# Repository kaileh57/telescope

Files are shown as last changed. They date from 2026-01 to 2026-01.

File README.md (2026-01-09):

# DIY Newtonian Reflector Telescope

I designed my own telescope!

This is a pretty simple Newtonian Reflector style telescope, with a 114mm primary mirror, and a 25mm secondary mirror. I'm making it because I really love taking pictures of the stars, and was able to do some cool stuff a few weeks ago with a telescope at a family member's house! Hopefully this is a (comparatively) low cost way of getting into the field. There's a couple of great dark sky spots near me (Seattle), and hopefully I can update with some awesome pictures.

Hopefully, I can get some pretty cool images of galaxies and other cool objects, and I've included a barlow lens which should help with planetary photography.

I designed as much as possible myself! Unfortunately I don't have the capabilities to make motors or precision optics, and I'm using a modified version of the Crayford Focuser, as I'm not experienced enough with precision optics.

Crayford focuser: https://www.printables.com/model/125438-125-crayford-focuser-for-telescopes/files

## Assembly

PCB:




CAD:


Annotated CAD:

Azimuth and Altitude motors are connected to the PCB box via pre crimped cables, the Altitude cable should have a significant amount of lose cabling in order to accomodate the rotation of the base. 
The Raspberry PI HQ Camera is mounted to the end of the focuser, and should be attached via ribbon cable to the Raspberry PI Zero 2 W in the electronics enclosure, which is connected to the power management PCB. 
The GPS module should be plugged in to its header on the PCB, and should be placed in a location where it has a good view of the sky, for my configuration, it will be mounted on the side of a truck, and therefor is not practical to include in the CAD model. 
12v DC power comes in to the PCB from the side. 

Approximate limit switch positions, the model here is similar but not identical to the model I already have and am planning to install. The limit switches are wired into the appropriate port on the PCB and are used in calibration so that the telescope knows where its facing. 

Annotated Diagram:
Untitled drawing

**Telescope Focuser**: The 1.25" Crayford focuser design is from [aeberbach on Printables](https://www.printables.com/model/118575-125-crayford-focuser-for-telescopes), licensed under CC BY-NC 4.0.

## License

### Modified MIT License

```
MIT License (with exception)
Copyright (c) 2026 Kellen Heraty

Permission is hereby granted, free of charge, to any person obtaining a copy
of this software and associated documentation files (the "Software"), to deal
in the Software without restriction, including without limitation the rights
to use, copy, modify, merge, publish, distribute, sublicense, and/or sell
copies of the Software, and to permit persons to whom the Software is
furnished to do so, subject to the following conditions:

The above copyright notice and this permission notice shall be included in all
copies or substantial portions of the Software.

EXCEPTION: This license does NOT apply to the 1.25" Crayford focuser design 
files (STL and STEP files in the /focuser directory), which are provided by 
aeberbach under Creative Commons Attribution-NonCommercial 4.0 International 
License (CC BY-NC 4.0). Those files may not be used for commercial purposes.

THE SOFTWARE IS PROVIDED "AS IS", WITHOUT WARRANTY OF ANY KIND, EXPRESS OR
IMPLIED, INCLUDING BUT NOT LIMITED TO THE WARRANTIES OF MERCHANTABILITY,
FITNESS FOR A PARTICULAR PURPOSE AND NONINFRINGEMENT. IN NO EVENT SHALL THE
AUTHORS OR COPYRIGHT HOLDERS BE LIABLE FOR ANY CLAIM, DAMAGES OR OTHER
LIABILITY, WHETHER IN AN ACTION OF CONTRACT, TORT OR OTHERWISE, ARISING FROM,
OUT OF OR IN CONNECTION WITH THE SOFTWARE OR THE USE OR OTHER DEALINGS IN THE
SOFTWARE.
```

## Bill of Materials

### Optics & Camera System

| Category | Item | Qty | Specification | Source | Est. Cost | Link |
|---|---|-----|---|---|---|---|
| Optics | Primary Mirror (spherical) | 1 | 114mm diameter, f/8 (912mm FL), enhanced aluminum coating, BK7 glass, 14mm thick | AliExpress | $25.20 | [Link](https://www.aliexpress.us/item/3256802406856110.html) |
| Optics | Secondary Mirror (flat diagonal) | 1 | 25 minor axis, flat, enhanced aluminum coating | AliExpress | Included | Bundled with primary mirror set |
| Camera | Pi HQ Camera | 1 | Sony IMX477, 12.3MP, C-mount thread | Digikey | $50.00 | [Link](https://www.pishop.us/product/raspberry-pi-hq-camera-cs/?src=raspberrypi) |
| Camera | CSI cable (adapter) | 1 | 500mm length, 22-pin (0.5mm pitch) to 15-pin (1.0mm pitch) | AliExpress | $4.55 | [Link](https://www.aliexpress.us/item/3256808091724799.html) |
| Camera | C-mount to 1.25" adapter | 1 | Short profile, screws onto C-mount, 1.25" barrel slides into focuser | AliExpress | $2.84 | [Link](https://www.aliexpress.us/item/3256803470616922.html) |
| Accessory | 2x Barlow lens with T-ring | 1 | 1.25" barrel, 2x magnification, M42×0.75 T-thread for DSLR | AliExpress | $10.85 | [Link](https://www.aliexpress.us/item/3256802185717221.html) |

### OTA Tube Assembly & Mirror Cell

| Category | Item | Qty | Specification | Source | Est. Cost | Link |
|---|---|-----|---|---|---|---|
| OTA Hardware | Alignment dowel pins | 9 | M3×10mm steel, precision | Hardware Store | $4.00 | M3x10 dowel pins |
| OTA Hardware | Interior flocking material | 1 | Self-adhesive black velvet or flocking paper, ~900×450mm | AliExpress | $8.86 | [Link](https://www.aliexpress.us/item/3256807322733280.html) |
| Mirror Cell | Collimation bolts | 3 | M4×50mm hex head | Hardware Store | $5.00 | M4x50mm hex bolts |
| Mirror Cell | Compression springs | 3 | 0.5mm wire, 5mm od, 10mm long | Hardware Store | $4.00 | Between floor and floating plate for push-pull collimation |
| Mirror Cell | Flat washers (M4) | 6 | M4 size | Hardware Store | $2.00 | Top and bottom of each spring M4x9x0.5 |
| Mirror Cell | Wing nuts | 3 | M4 thread | Hardware Store | $3.50 | Hand-adjustable collimation from below |
| Mirror Cell | Cell mounting screws | 6 | M3×16mm socket head | Hardware Store | $4.50 | Attach cell housing to Segment 1 |
| Mirror Cell | Heat-set inserts (M3) | 6 | M3×6mm×5mm | Hardware Store | $6.00 | Press into Segment 1 for cell mounting |
| Mirror Cell | RTV Silicone | 1 | Sealant | AliExpress | $2.96 | [Link](https://www.aliexpress.us/item/3256807120493463.html) |
| Mirror Cell | Epoxy or super glue | 1 | Small tube | AliExpress | $2.31 | [Link](https://www.aliexpress.us/item/3256809235639574.html) |

### Secondary Spider Assembly

| Category | Item | Qty | Specification | Source | Est. Cost | Link |
|---|---|-----|---|---|---|---|
| Spider | Spider mounting screws | 4 | M3×16mm socket head | - | Included above | Mount spider ring to Segment 4 (through tube wall at 45° offsets) |
| Spider | Spider mounting nuts | 4 | M3 hex nuts | Hardware Store | $2.00 | M3 hex nuts for spider mounting |
| Spider | Secondary mirror adhesive | 1 | RTV silicone | - | Included above | Bonds secondary to 45° holder surface |

### Mount Structure

| Category | Item | Qty | Specification | Source | Est. Cost | Link |
|---|---|-----|---|---|---|---|
| Mount | Tube ring clamp bolts | 2 | M5×50mm hex head | Hardware Store | $4.00 | Clamp tube rings around OTA m5x50 |
| Mount | Tube ring to cradle bolts | 4 | M5×50mm hex head | - | Included above | Attach rings to altitude cradle |
| Mount | Fork to turntable bolts | 4 | M5×25mm socket head | Hardware Store | $3.50 | Secure forks to turntable |
| Mount | M5 nuts | 6 | Standard hex nuts | Hardware Store | $2.50 | For clamp and cradle bolts |
| Mount | M5 washers | 16 | Flat washers | Hardware Store | $3.00 | Under bolt heads and nuts |
| Mount | Heat-set inserts (M5) | 4 | M5 size | Hardware Store | $6.00 | In turntable for fork mounting |
| Mount | Hex nut (1/4-20) | 1 | 1/4-20 UNC thread | Hardware Store | $1.50 | Tripod mount in base center |
| Mount | Felt/foam tape | 1 | Self-adhesive, ~25mm wide roll | AliExpress | $2.24 | [Link](https://www.aliexpress.us/item/3256807381928957.html) |
| Mount | Lazy susan mounting screws | 8 | M4×12mm | Hardware Store | $4.00 | 4 per ring of lazy susan bearing |
| Mount | M4 nuts | 4 | Standard hex nuts | Hardware Store | $2.00 | Inner ring of lazy susan (through-hole to base) |

### Bearings

| Category | Item | Qty | Specification | Source | Est. Cost | Link |
|---|---|-----|---|---|---|---|
| Bearing | 608ZZ bearing | 1 | 8mm ID × 22mm OD × 7mm thick | AliExpress | $4.23 | [Link](https://www.aliexpress.us/item/3256805135171835.html) |
| Bearing | Lazy Susan bearing (Profile B) | 1 | 120mm OD, 79mm ID, 8.5mm thick, aluminum, PCD: 91.8mm inner / 109mm outer | AliExpress | $6.69 | [Link](https://www.aliexpress.us/item/3256807353712714.) |

### Drive Systems

| Category | Item | Qty | Specification | Source | Est. Cost | Link |
|---|---|-----|---|---|---|---|
| Alt Drive | NEMA17 Worm Gear Motor (1:32) | 1 | RobotDigg, 42×42×48mm motor + 40×58×27mm gearbox, 8mm D-shaft output, 1.8Nm torque, 1.7A | AliExpress | $28.06 | [Link](https://www.aliexpress.us/item/3256808139356937.html) |
| Alt Drive | Shaft coupler (8mm-8mm) | 1 | Aluminum, ~25mm body length | AliExpress | $3.49 | [Link](https://www.aliexpress.us/item/3256805451220598.html) |
| Alt Drive | Motor mount screws | 4 | M4×10mm flat head | Hardware Store | $3.00 | - |
| Alt Drive | Mount plate screws | 4 | M4×20mm socket head | Hardware Store | $3.50 | Attach motor mount plate to left fork |
| Az Drive | NEMA17 Worm Gear Motor (1:32) | 1 | RobotDigg, same spec as altitude motor | AliExpress | $28.06 | [Link](https://www.aliexpress.us/item/3256808139356937.html) |
| Az Drive | GT2 timing belt (6mm) | 1 | ~800mm length, open-ended, cut to fit | AliExpress | $8.48 | [Link](https://www.aliexpress.us/item/3256802121511505.html) |
| Az Drive | GT2 pulley (30T) | 1 | 30 teeth, 8mm bore, 6mm belt width | AliExpress | $3.65 | [Link](https://www.aliexpress.us/item/3256805593092055.html) |
| Az Drive | Motor mount screws | 4 | M4×12mm flat head | - | Included above | Through slotted holes in base extension tab |

### PCB Through-Hole Components

| Category | Item | Qty | Specification | Source | Est. Cost | Link |
|---|---|-----|---|---|---|---|
| PCB TH | 100µF 25V electrolytic capacitor | 3 | Through-hole, radial | AliExpress | $2.32 | [Link](https://www.aliexpress.us/item/3256805247425905.html) |
| PCB TH | 220µF 10V electrolytic capacitor | 1 | Through-hole, radial | AliExpress | $2.15 | [Link](https://www.aliexpress.us/item/3256805247425905.html) |
| PCB TH | 2×20 female header | 1 | 2.54mm pitch, through-hole | AliExpress | $1.42 | [Link](https://www.aliexpress.us/item/2251832667900858.html) |
| PCB TH | 1×8 female header | 4 | 2.54mm pitch, through-hole | AliExpress | $1.61 | [Link](https://www.aliexpress.us/item/2255801012106911.html) |
| PCB TH | JST-XH 4-pin connector | 2 | Vertical | - | Included with pigtails kit | Motor output connectors (J_MOT1, J_MOT2) |
| PCB TH | DC barrel jack | 1 | 5.5×2.1mm, center positive | Digikey | $0.64 | [Link](https://www.digikey.com/en/products/detail/same-sky-formerly-cui-devices/PJ-002AH/408446) |

### Electronics Modules

| Category | Item | Qty | Specification | Source | Est. Cost | Link |
|---|---|-----|---|---|---|---|
| Module | Raspberry Pi Zero 2 W | 1 | PI zero 2 w | Digikey | $15.00 | [Link](https://www.digikey.com/en/products/detail/raspberry-pi/SC1176/15298147) |
| Module | TMC2209 StepStick | 2 | BIGTREETECH V1.2 or V1.3 | AliExpress | $9.72 | [Link](https://www.aliexpress.us/item/2255800257311131.html) |
| Module | NEO-6M GPS module | 1 | 3.3V logic output ONLY - 5V will damage Pi! | AliExpress | $8.90 | [Link](https://www.aliexpress.us/item/3256808037885086.html) |
| Module | MP1584 buck converter module | 1 | Adjustable output, set to 5.0-5.1V, needs to be adjustable for precision | AliExpress | $1.57 | [Link](https://www.aliexpress.us/item/3256808313082613.html) |
| Wiring | 22awg wire | 20cm | For connecting MP1584, hard to find in small quantities | AliExpress | $3.04 | [Link](https://www.aliexpress.us/item/3256808757002563.html) |
| Module | 10×10mm heatsinks | 4 | Aluminum, with thermal adhesive tape | AliExpress | $3.94 | [Link](https://www.aliexpress.us/item/3256804749177306.html) |

### Power & Wiring

| Category | Item | Qty | Specification | Source | Est. Cost | Link |
|---|---|-----|---|---|---|---|
| Power | 12V 5A DC power supply | 1 | 5.5×2.1mm barrel jack output, center positive | AliExpress | $17.22 | [Link](https://www.aliexpress.us/item/3256807351095066.html) |
| Wiring | JST-XH 4-pin pigtails | 4 | Pre-crimped leads, ~30cm | AliExpress | $7.13 | [Link](https://www.aliexpress.us/item/3256808528022826.html) |
| Wiring | Heat shrink tubing | 1 | Assorted sizes kit | - | Included | Insulate splices |
| Wiring | Motor cables | 2 | 4-wire, ~50cm, usually included with motors | With motors | Included | Check if included with RobotDigg motors |
| Wiring | Motor extension | 2 | Allows the cables to reach | AliExpress | $6.05 | [Link](https://www.aliexpress.us/item/3256807018820517.html) |

### Accessories

| Category | Item | Qty | Specification | Source | Est. Cost | Link |
|---|---|-----|---|---|---|---|
| Accessory | Rubber friction pads | 4 | Self-adhesive | AliExpress | $2.18 | [Link](https://www.aliexpress.us/item/3256806771014461.html) |

### Focuser Components

| Category | Item | Qty | Specification | Source | Est. Cost | Link |
|---|---|-----|---|---|---|---|
| Motion | MR83ZZ bearings | 4 | 3mm ID × 8mm OD × 3mm thick | AliExpress | $5.24 | [Link](https://www.aliexpress.us/item/3256804648772069.html) |
| Motion | Steel shaft | 1 | 5mm diameter × 90mm length, stainless | AliExpress | $2.31 | [Link](https://www.aliexpress.us/item/3256805290944526.html) |
| Motion | Aluminum flat bar | 1 | 10mm × 3mm × 150mm (cut 64+64+37 = 165mm needed) | AliExpress | $3.52 | [Link](https://www.aliexpress.us/item/3256805124428430.html) |
| Motion | Compression springs | 2 | OD < 5mm, ~6.5mm length, STIFF (not pen springs) | Hardware Store | $3.00 | Small compression springs |
| Inserts | M3 heat-set inserts | 8 | M3 × 5mm L × 4.5mm OD | Hardware Store | $8.00 | M3 heat-set inserts |
| Inserts | M4 heat-set inserts | 4 | M4 × 6mm L × 5.5mm OD | Hardware Store | $6.00 | M4 heat-set inserts |
| Bolts | M3×10mm button head | 4 | Button head, bearing axles | Hardware Store | $3.00 | Button head screws for bearing axles |
| Bolts | M3×12mm socket head | 4 | Socket head, drawtube cap | Hardware Store | $3.00 | Socket head for drawtube cap |
| Bolts | M3×20mm socket head | 4 | Socket head, front cap to base | Hardware Store | $3.50 | Socket head for front cap |
| Bolts | M4×12mm socket head | 4 | Socket head, mount focuser to telescope | - | Included above | - |
| Nuts | M3 nylock nuts | 4 | Nylon insert lock nuts, secure bearing axles | Hardware Store | $2.50 | Nylock nuts for bearing security |
| Nuts | M3 hex nut | 1 | Standard, pressed into front cap for tension screw | - | Included above | - |
| Nuts | M3 thumbscrew | 1 | Knurled head, main tension adjustment | Hardware Store | $3.00 | Knurled thumbscrew for tension |
| Nuts | M3 set screws | 2 | Grub screws | Hardware Store | $2.00 | - |

### 3D Printed Components

Hoping to print all from the same person, near me in Seattle. Mostly PETG, some PLA, TPU would be cool but not needed at all.

| Component | Material | Infill | Est. Print Time | Notes |
|---|---|---|---|---|
| **OTA - Tube Assembly** |
| Tube_Segment_1 (rear) | PETG | 30% gyroid | ~12 hours | Mirror cell interface, 220mm length, 130mm ID, 4mm wall |
| Tube_Segment_2 | PETG | 30% gyroid | ~12 hours | Middle segment, alignment pins at joints |
| Tube_Segment_3 | PETG | 30% gyroid | ~12 hours | Middle segment |
| Tube_Segment_4 (front) | PETG | 30% gyroid | ~12 hours | Focuser boss (70×70mm), spider mount holes at 45° offset |
| **OTA - Mirror Cell (Hadley-style)** |
| Primary_Mirror_Cell_Housing | PETG | 30% | ~8 hours | 154mm OD flange, 120mm ID wall, floor with 40mm vent, 3× spring bosses |
| Floating_Plate | PETG | 30% | ~2 hours | 118mm OD × 8mm, hex pockets for bolt capture, 115mm mirror recess |
| **OTA - Secondary Assembly** |
| Secondary_Spider | PLA or PETG | 40% | ~4 hours | 4-vane design, ring fits inside tube top, 45° mirror holder, 3× collimation screws |
| **OTA - Focuser (aeberbach Crayford - Printables #125438)** |
| Focuser_Body | PETG | 40% | ~2.5 hours | Main body with 4× bearing mounts, 4× M3 insert holes for front cap |
| Pinion_Block | PETG | 40% | ~30 min | Shaft passes through; 2× spring holes in back for tension |
| Front_Cap | PETG | 40% | ~45 min | Recess for M3 hex nut (tension screw); mounts with 4× M3×20mm |
| Drawtube | PETG | 30% | ~1.5 hours | Print flange-down; slots for 2× 64mm aluminum strips |
| Drawtube_Cap | PETG | 30% | ~30 min | Print flange-down; secures aluminum strips; 4× M3×12mm + M3 inserts |
| Pinion_Spacer (×2) | PETG | 30% | ~15 min total | Covers exposed shaft ends outside body |
| Focus_Knob (×2) | PETG | 30% | ~30 min total | Small knob(s) |
| **OTA - Dust Covers** |
| Front_Dust_Cap | PLA or PETG | 20% | ~1 hour | 139mm ID, 145mm OD, 15mm tall with pull tab |
| Rear_Dust_Cover | PLA or PETG | 20% | ~1 hour | 160mm OD disc with 154/148mm retention ring |
| Focuser_Cap | PLA | 20% | ~15 min | 31.5mm plug, 38mm flange, friction fit |
| **Mount - Tube Rings & Cradle** |
| Tube_Ring (×2) | PETG | 30% | ~4 hours total | 148mm OD, 140mm ID, split clamp, mounting boss for cradle |
| Altitude_Cradle | PETG | 30% | ~3 hours | 200×80×8mm plate, LEFT shaft 45mm (motor side), RIGHT shaft 25mm |
| **Mount - Forks** |
| Altitude_Fork_LEFT | PETG | 30% | ~8 hours | 60×120×15mm, 4× M4 heat-set holes for motor mount plate |
| Altitude_Fork_RIGHT | PETG | 30% | ~8 hours | 60×120×15mm, 608ZZ bearing pocket for pivot |
| Alt_Motor_Mount_Plate | PETG | 30% | ~1 hour | 60×60×5mm, NEMA17 pattern, 25mm center clearance hole |
| **Mount - Azimuth Base** |
| Azimuth_Stationary_Base | PETG | 25% | ~12 hours | 280mm dia + motor extension tab (80×70×8mm), tripod mount, lazy susan PCD 91.8mm |
| Azimuth_Turntable | PETG | 25% | ~6 hours | 220mm OD, 80mm center hole, lazy susan PCD 109mm, fork mounting bosses |
| Base_Feet (×4) | PETG or TPU | 30% | ~2 hours | ~40mm tall for gearbox clearance, rubber pad attachment |
| **Electronics** |
| Electronics_Enclosure | PLA | 20% | ~6 hours | Box for PCB + Pi Zero, ventilation slots, friction-fit lid |

### PCB SMT Components (JLCPCB Assembly)

| Designator | Value/Part | LCSC# | Qty/Board | Ext (2 boards) | Notes |
|---|---|---|---|---|---|
| C3 | 22uF 16V Tantalum | C782264 | 1 | $0.67 | Extended |
| C4,C7,C8,C9,C10,C11 | 100nF 0603 | C14663 | 6 | $0.17 | Basic (6× ~$0.03) |
| D1 | 6.8V Zener SOD-123 | C2120 | 1 | $0.26 | Extended |
| F1 | 4A Polyfuse 2920 | C139284 | 1 | $0.61 | Littelfuse Extended |
| F2 | 1.5A Polyfuse 1206 | C70083 | 1 | $0.33 | TECHFUSE Extended |
| Q1 | AO3401A P-FET | C15127 | 1 | $0.11 | Basic |
| R1,R2,R3 | 10k 0603 | C25804 | 3 | $0.02 | Basic |
| U1 | AMS1117-3.3 | C6186 | 1 | $0.32 | Basic |

**SMT Total: $2.49** (from JLCPCB quote)

### Cost Summary

| Source | Total |
|---|---|
| Digikey | $72.69 |
| AliExpress | $285.26 |
| Hardware Store | I will pay/find these parts |
| JLCPCB | $45.71 |
| **Total** | **$403.66** |

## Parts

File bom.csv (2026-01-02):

Category | Item | Qty | Specification | Source | Est. Cost (not incl Shipping or tax) | Link/Notes
OPTICS
Optics | Primary Mirror (spherical) | 1 | 114mm diameter, f/8 (912mm FL), enhanced aluminum coating, BK7 glass, 14mm thick | AliExpress | $25.20 | spherical is much cheaper than parabolic, but slightly worse https://www.aliexpress.us/item/3256802406856110.html
Optics | Secondary Mirror (flat diagonal) | 1 | 25 minor axis, flat, enhanced aluminum coating | AliExpress | Included | Bundled with primary mirror set
CAMERA SYSTEM
Camera | Pi HQ Camera | 1 | Sony IMX477, 12.3MP, C-mount thread | Digikey | $50.00 | https://www.pishop.us/product/raspberry-pi-hq-camera-cs/?src=raspberrypi | SC
Camera | CSI cable (adapter) | 1 | 500mm length, 22-pin (0.5mm pitch) to 15-pin (1.0mm pitch) | AliExpress | $4.55 | 500mm version https://www.aliexpress.us/item/3256808091724799.html
Camera | C-mount to 1.25" adapter | 1 | Short profile, screws onto C-mount, 1.25" barrel slides into focuser | AliExpress | $2.84 | https://www.aliexpress.us/item/3256803470616922.html?
OPTICAL ACCESSORIES
Accessory | 2x Barlow lens with T-ring | 1 | 1.25" barrel, 2x magnification, M42×0.75 T-thread for DSLR | AliExpress | $10.85 | massively helps with planetary imaging https://www.aliexpress.us/item/3256802185717221.html
OTA TUBE ASSEMBLY
OTA Hardware | Alignment dowel pins | 9 | M3×10mm steel, precision | Hardware Store | $4.00 | m3x10 dowel pins
OTA Hardware | Interior flocking material | 1 | Self-adhesive black velvet or flocking paper, ~900×450mm | AliExpress | $8.86 | 45cm x 10m https://www.aliexpress.us/item/3256807322733280.html
PRIMARY MIRROR CELL
Mirror Cell | Collimation bolts | 3 | M4×50mm hex head | Hardware Store | $5.00 | m4x50mm hex bolts
Mirror Cell | Compression springs | 3 | 0.5mm wire, 5mm od, 10mm long | Hardware Store | $4.00 | Between floor and floating plate for push-pull collimation: 0.5mm wire, 5mm od, 10mm long
Mirror Cell | Flat washers (M4) | 6 | M4 size | Hardware Store | $2.00 | Top and bottom of each spring M4x9x0.5
Mirror Cell | Wing nuts | 3 | M4 thread | Hardware Store | $3.50 | Hand-adjustable collimation from below
Mirror Cell | Cell mounting screws | 6 | M3×16mm socket head | Hardware Store | $4.50 | Attach cell housing to Segment 1
Mirror Cell | Heat-set inserts (M3) | 6 | M3×6mm×5mm | Hardware Store | $6.00 | Press into Segment 1 for cell mounting
Mirror Cell | RTV Silicone | 1 | Sealant | AliExpress | $2.96 | Bonds mirror to floating plate; flexible for thermal expansion, https://www.aliexpress.us/item/3256807120493463.html
Mirror Cell | Epoxy or super glue | 1 | Small tube | AliExpress | $2.31 | Permanently captures M4 bolt heads in hex pockets https://www.aliexpress.us/item/3256809235639574.html
SECONDARY SPIDER ASSEMBLY
Spider | Spider mounting screws | 4 | M3×16mm socket head |  | Included above | Mount spider ring to Segment 4 (through tube wall at 45° offsets)
Spider | Spider mounting nuts | 4 | M3 hex nuts | Hardware Store | $2.00 | M3 hex nuts for spider mounting
Spider | Secondary mirror adhesive | 1 | RTV silicone |  | Included above | Bonds secondary to 45° holder surface
MOUNT STRUCTURE
Mount | Tube ring clamp bolts | 2 | M5×50mm hex head | Hardware Store | $4.00 | Clamp tube rings around OTA m5x50
Mount | Tube ring to cradle bolts | 4 | M5×50mm hex head |  | Included above | Attach rings to altitude cradle
Mount | Fork to turntable bolts | 4 | M5×25mm socket head | Hardware Store | $3.50 | Secure forks to turntable
Mount | M5 nuts | 6 | Standard hex nuts | Hardware Store | $2.50 | For clamp and cradle bolts
Mount | M5 washers | 16 | Flat washers | Hardware Store | $3.00 | Under bolt heads and nuts
Mount | Heat-set inserts (M5) | 4 | M5 size | Hardware Store | $6.00 | In turntable for fork mounting
Mount | Hex nut (1/4-20) | 1 | 1/4-20 UNC thread | Hardware Store | $1.50 | Tripod mount in base center
Mount | Felt/foam tape | 1 | Self-adhesive, ~25mm wide roll | AliExpress | $2.24 | Line inside of tube rings to protect OTA, general adhesive, 25mm https://www.aliexpress.us/item/3256807381928957.html
Mount | Lazy susan mounting screws | 8 | M4×12mm | Hardware Store | $4.00 | 4 per ring of lazy susan bearing
Mount | M4 nuts | 4 | Standard hex nuts | Hardware Store | $2.00 | Inner ring of lazy susan (through-hole to base)
BEARINGS
Bearing | 608ZZ bearing | 1 | 8mm ID × 22mm OD × 7mm thick | AliExpress | $4.23 | Altitude pivot (non-motor side, right fork), https://www.aliexpress.us/item/3256805135171835.html
Bearing | Lazy Susan bearing (Profile B) | 1 | 120mm OD, 79mm ID, 8.5mm thick, aluminum, PCD: 91.8mm inner / 109mm outer | AliExpress | $6.69 | Azimuth rotation; https://www.aliexpress.us/item/3256807353712714.
ALTITUDE DRIVE SYSTEM
Alt Drive | NEMA17 Worm Gear Motor (1:32) | 1 | RobotDigg, 42×42×48mm motor + 40×58×27mm gearbox, 8mm D-shaft output, 1.8Nm torque, 1.7A | robotdigg.com | $28.06 | https://www.aliexpress.us/item/3256808139356937.html
Alt Drive | Shaft coupler (8mm-8mm) | 1 | Aluminum, ~25mm body length | AliExpress | $3.49 | Connects motor shaft to cradle pivot shaft, 8x8 https://www.aliexpress.us/item/3256805451220598.html
Alt Drive | Motor mount screws | 4 | M4×10mm flat head | Hardware Store | $3.00
Alt Drive | Mount plate screws | 4 | M4×20mm socket head | Hardware Store | $3.50 | Attach motor mount plate to left fork
AZIMUTH DRIVE SYSTEM
Az Drive | NEMA17 Worm Gear Motor (1:32) | 1 | RobotDigg, same spec as altitude motor | robotdigg.com | $28.06 | https://www.aliexpress.us/item/3256808139356937.html
Az Drive | GT2 timing belt (6mm) | 1 | ~800mm length, open-ended, cut to fit | AliExpress | $8.48 | Wraps around 220mm turntable edge (~690mm circumference), 1m, 6mm width, https://www.aliexpress.us/item/3256802121511505.html
Az Drive | GT2 pulley (30T) | 1 | 30 teeth, 8mm bore, 6mm belt width | AliExpress | $3.65 | Mounts on shaft extension above motor, 30 teeth, 6mm, 8mm bore https://www.aliexpress.us/item/3256805593092055.html
Az Drive | Motor mount screws | 4 | M4×12mm flat head, needs to be flat head for clearance |  | Included above | Through slotted holes in base extension tab
PCB - THROUGH-HOLE COMPONENTS
PCB TH | 100µF 25V electrolytic capacitor | 3 | Through-hole, radial | AliExpress | $2.32 | 1× input bulk + 2× TMC2209 VMOT 25v100uf 6x11 https://www.aliexpress.us/item/3256805247425905.html
PCB TH | 220µF 10V electrolytic capacitor | 1 | Through-hole, radial | AliExpress | $2.15 | 5V rail bulk near Pi header, 10v220uf 5x11 https://www.aliexpress.us/item/3256805247425905.html
PCB TH | 2×20 female header | 1 | 2.54mm pitch, through-hole | AliExpress | $1.42 | Pi Zero socket 1x20pin https://www.aliexpress.us/item/2251832667900858.html
PCB TH | 1×8 female header | 4 | 2.54mm pitch, through-hole | AliExpress | $1.61 | TMC2209 StepStick sockets 1x8pin https://www.aliexpress.us/item/2255801012106911.html
PCB TH | JST-XH 4-pin connector | 2 | vertical |  | Included with pigtails kit | Motor output connectors (J_MOT1, J_MOT2)
PCB TH | DC barrel jack | 1 | 5.5×2.1mm, center positive | Digikey | $0.64 | MUST be from a reliable distributer as we need 12v 5a https://www.digikey.com/en/products/detail/same-sky-formerly-cui-devices/PJ-002AH/408446
ELECTRONICS - MODULES
Module | Raspberry Pi Zero 2 W | 1 | PI zero 2 w | Digikey | $15.00 | Main controller - camera, GPS, motor control, https://www.digikey.com/en/products/detail/raspberry-pi/SC1176/15298147
Module | TMC2209 StepStick | 2 | BIGTREETECH V1.2 or V1.3 | AliExpress | $9.72 | Stepper drivers, 2A max, STEP/DIR mode https://www.aliexpress.us/item/2255800257311131.html
Module | NEO-6M GPS module | 1 | 3.3V logic output ONLY - 5V will damage Pi! | AliExpress | $8.90 | Position and time sync for GoTo https://www.aliexpress.us/item/3256808037885086.html
Module | MP1584 buck converter module | 1 | Adjustable output, set to 5.0-5.1V, needs to be adjustable for precision | AliExpress | $1.57 | 12V to 5V for Pi Zero https://www.aliexpress.us/item/3256808313082613.html
Wiring | 22awg wire | 20cm | For connecting MP1584, hard to find in small quantities | AliExpress | $3.04 | 22 awg https://www.aliexpress.us/item/3256808757002563.html
Module | 10×10mm heatsinks | 4 | Aluminum, with thermal adhesive tape | AliExpress | $3.94 | 1× MP1584 (mandatory!) + 1 for pi + 2× TMC2209 (in case they dont include it) https://www.aliexpress.us/item/3256804749177306.html
POWER
Power | 12V 5A DC power supply | 1 | 5.5×2.1mm barrel jack output, center positive | AliExpress | $17.22 | Minimum 5A for motor peak current headroom, grounded! GST60A12-P1J https://www.aliexpress.us/item/3256807351095066.html
WIRING & CABLES
Wiring | JST-XH 4-pin pigtails | 4 | Pre-crimped leads, ~30cm | AliExpress | $7.13 | https://www.aliexpress.us/item/3256808528022826.html
Wiring | Heat shrink tubing | 1 | Assorted sizes kit |  | included | Insulate splices
Wiring | Motor cables | 2 | 4-wire, ~50cm, usually included with motors | With motors | included | Check if included with RobotDigg motors
Wiring | Motor extension | 2 | allows the cables to reach | AliExpress | $6.05 | https://www.aliexpress.us/item/3256807018820517.html
ACCESSORIES
Accessory | Rubber friction pads | 4 | Self-adhesive | AliExpress | $2.18 | Base feet for stability https://www.aliexpress.us/item/3256806771014461.html
FOCUSER
Motion | MR83ZZ bearings | 4 | 3mm ID × 8mm OD × 3mm thick | AliExpress | $5.24 | Mr83zz 3x8x3mm, order 4, https://www.aliexpress.us/item/3256804648772069.html
Motion | Steel shaft | 1 | 5mm diameter × 90mm length, stainless | AliExpress | $2.31 | 125mm, 5mm diameter https://www.aliexpress.us/item/3256805290944526.html
Motion | Aluminum flat bar | 1 | 10mm × 3mm × 150mm (cut 64+64+37 = 165mm needed) | AliExpress | $3.52 | 3 x 10 x 300mm https://www.aliexpress.us/item/3256805124428430.html
Motion | Compression springs | 2 | OD < 5mm, ~6.5mm length, STIFF (not pen springs) | Hardware Store | $3.00 | Small compression springs
Inserts | M3 heat-set inserts | 8 | M3 × 5mm L × 4.5mm OD | Hardware Store | $8.00 | M3 heat-set inserts
Inserts | M4 heat-set inserts | 4 | M4 × 6mm L × 5.5mm OD | Hardware Store | $6.00 | M4 heat-set inserts
Bolts | M3×10mm button head | 4 | Button head, bearing axles | Hardware Store | $3.00 | Button head screws for bearing axles
Bolts | M3×12mm socket head | 4 | Socket head, drawtube cap | Hardware Store | $3.00 | Socket head for drawtube cap
Bolts | M3×20mm socket head | 4 | Socket head, front cap to base | Hardware Store | $3.50 | Socket head for front cap
Bolts | M4×12mm socket head | 4 | Socket head, mount focuser to telescope |  | Included above
Nuts | M3 nylock nuts | 4 | Nylon insert lock nuts, secure bearing axles | Hardware Store | $2.50 | Nylock nuts for bearing security
Nuts | M3 hex nut | 1 | Standard, pressed into front cap for tension screw |  | Included above
Nuts | M3 thumbscrew | 1 | Knurled head, main tension adjustment | Hardware Store | $3.00 | Knurled thumbscrew for tension
Nuts | M3 set screws (grub) | 2 | Secures printed knobs to 5mm shaft | Hardware Store | $2.00 | Set screws for knob attachment
HARDWARE STORE TOTALS
HARDWARE STORE TOTALS
 | Alignment dowel pins | 9 | M3×10mm | Hardware Store | $4.00
 | Collimation bolts | 3 | M4×50mm | Hardware Store | $5.00
 | Compression springs (mirror cell) | 3 | 0.5mm wire 5mm od | Hardware Store | $4.00
 | Flat washers M4 | 6 | M4 | Hardware Store | $2.00
 | Wing nuts | 3 | M4 | Hardware Store | $3.50
 | Cell mounting screws | 10 | M3×16mm socket head | Hardware Store | $4.50
 | Heat-set inserts M3 (cell) | 6 | M3×6mm×5mm | Hardware Store | $6.00
 | Spider mounting nuts | 5 | M3 hex nuts | Hardware Store | $2.00
 | Tube ring clamp bolts | 6 | M5×50mm hex head | Hardware Store | $4.00
 | Fork to turntable bolts | 4 | M5×25mm | Hardware Store | $3.50
 | M5 nuts | 6 | Standard hex | Hardware Store | $2.50
 | M5 washers | 16 | Flat | Hardware Store | $3.00
 | Heat-set inserts M5 | 4 | M5 | Hardware Store | $6.00
 | Hex nut 1/4-20 | 1 | 1/4-20 UNC | Hardware Store | $1.50
 | Lazy susan mounting screws | 8 | M4×12mm | Hardware Store | $4.00
 | M4 nuts | 4 | Standard hex | Hardware Store | $2.00
 | Motor mount screws (alt) | 4 | M4×10mm flat head | Hardware Store | $3.00
 | Motor mount screws (az) | 4 | M4×12mm flat head | Hardware Store | $3.00
 | Mount plate screws | 4 | M4×20mm | Hardware Store | $3.50
 | Compression springs (focuser) | 2 | OD < 5mm | Hardware Store | $3.00
 | M3 heat-set inserts (focuser) | 8 | M3×5mm | Hardware Store | $8.00
 | M4 heat-set inserts (focuser) | 4 | M4×6mm | Hardware Store | $6.00
 | M3×10mm button head | 4 | Button head | Hardware Store | $3.00
 | M3×12mm socket head | 4 | Socket head | Hardware Store | $3.00
 | M3×20mm socket head | 4 | Socket head | Hardware Store | $3.50
 | Focuser mount screws | 4 | M4×12mm socket head | Hardware Store | $3.00
 | M3 nylock nuts | 4 | Nylon insert | Hardware Store | $2.50
 | M3 thumbscrew | 1 | Knurled | Hardware Store | $3.00
 | M3 set screws | 2 | Grub screws | Hardware Store | $2.00
 | HARDWARE STORE TOTAL |  |  | $104.00 | I will pay/find these parts
3D PRINTING
Hoping to print all from the same person, near me in Seattle
Mostly PETG, some PLA, TPU would be cool but not needed at all
Component | Material | Infill | Est. Print Time | Notes
OTA - TUBE ASSEMBLY
Tube_Segment_1 (rear) | PETG | 30% gyroid | ~12 hours | Mirror cell interface, 220mm length, 130mm ID, 4mm wall
Tube_Segment_2 | PETG | 30% gyroid | ~12 hours | Middle segment, alignment pins at joints
Tube_Segment_3 | PETG | 30% gyroid | ~12 hours | Middle segment
Tube_Segment_4 (front) | PETG | 30% gyroid | ~12 hours | Focuser boss (70×70mm), spider mount holes at 45° offset
OTA - MIRROR CELL (Hadley-style)
Primary_Mirror_Cell_Housing | PETG | 30% | ~8 hours | 154mm OD flange, 120mm ID wall, floor with 40mm vent, 3× spring bosses
Floating_Plate | PETG | 30% | ~2 hours | 118mm OD × 8mm, hex pockets for bolt capture, 115mm mirror recess
OTA - SECONDARY ASSEMBLY
Secondary_Spider | PLA or PETG | 40% | ~4 hours | 4-vane design, ring fits inside tube top, 45° mirror holder, 3× collimation screws
OTA - FOCUSER (aeberbach Crayford - Printables #125438)
Focuser_Body | PETG | 40% | ~2.5 hours | Main body with 4× bearing mounts, 4× M3 insert holes for front cap
Pinion_Block | PETG | 40% | ~30 min | Shaft passes through; 2× spring holes in back for tension
Front_Cap | PETG | 40% | ~45 min | Recess for M3 hex nut (tension screw); mounts with 4× M3×20mm
Drawtube | PETG | 30% | ~1.5 hours | Print flange-down; slots for 2× 64mm aluminum strips
Drawtube_Cap | PETG | 30% | ~30 min | Print flange-down; secures aluminum strips; 4× M3×12mm + M3 inserts
Pinion_Spacer (×2) | PETG | 30% | ~15 min total | Covers exposed shaft ends outside body
Focus_Knob (×2) | PETG | 30% | ~30 min total | Small knob(s)
OTA - DUST COVERS
Front_Dust_Cap | PLA or PETG | 20% | ~1 hour | 139mm ID, 145mm OD, 15mm tall with pull tab
Rear_Dust_Cover | PLA or PETG | 20% | ~1 hour | 160mm OD disc with 154/148mm retention ring
Focuser_Cap | PLA | 20% | ~15 min | 31.5mm plug, 38mm flange, friction fit
MOUNT - TUBE RINGS & CRADLE
Tube_Ring (×2) | PETG | 30% | ~4 hours total | 148mm OD, 140mm ID, split clamp, mounting boss for cradle
Altitude_Cradle | PETG | 30% | ~3 hours | 200×80×8mm plate, LEFT shaft 45mm (motor side), RIGHT shaft 25mm
MOUNT - FORKS
Altitude_Fork_LEFT | PETG | 30% | ~8 hours | 60×120×15mm, 4× M4 heat-set holes for motor mount plate
Altitude_Fork_RIGHT | PETG | 30% | ~8 hours | 60×120×15mm, 608ZZ bearing pocket for pivot
Alt_Motor_Mount_Plate | PETG | 30% | ~1 hour | 60×60×5mm, NEMA17 pattern, 25mm center clearance hole
MOUNT - AZIMUTH BASE
Azimuth_Stationary_Base | PETG | 25% | ~12 hours | 280mm dia + motor extension tab (80×70×8mm), tripod mount, lazy susan PCD 91.8mm
Azimuth_Turntable | PETG | 25% | ~6 hours | 220mm OD, 80mm center hole, lazy susan PCD 109mm, fork mounting bosses
Base_Feet (×4) | PETG or TPU | 30% | ~2 hours | ~40mm tall for gearbox clearance, rubber pad attachment
ELECTRONICS
Electronics_Enclosure | PLA | 20% | ~6 hours | Box for PCB + Pi Zero, ventilation slots, friction-fit lid
PCB:
Category | Designator | Value/Part | LCSC# | Qty/Bd | Ext (2 bds) | Notes
JLCPCB SMT ASSEMBLY (2 boards)
SMT | C3 | 22uF 16V Tantalum | C782264 | 1 | $0.67 | Extended
SMT | C4,C7,C8,C9,C10,C11 | 100nF 0603 | C14663 | 6 | $0.17 | Basic (6× ~$0.03)
SMT | D1 | 6.8V Zener SOD-123 | C2120 | 1 | $0.26 | Extended
SMT | F1 | 4A Polyfuse 2920 | C139284 | 1 | $0.61 | Littelfuse Extended
SMT | F2 | 1.5A Polyfuse 1206 | C70083 | 1 | $0.33 | TECHFUSE Extended
SMT | Q1 | AO3401A P-FET | C15127 | 1 | $0.11 | Basic
SMT | R1,R2,R3 | 10k 0603 | C25804 | 3 | $0.02 | Basic
SMT | U1 | AMS1117-3.3 | C6186 | 1 | $0.32 | Basic
 |  |  |  | SMT Total: | $2.49 | From JLCPCB quote
HAND-SOLDER (in Main BOM - no extra cost)
TH Cap | C1,C5,C6 | 100uF 25V Electrolytic | - | 3 | - | Row 50: $2.32
TH Cap | C2 | 220uF 10V Electrolytic | - | 1 | - | Row 51: $2.15
Connector | J1 | DC Barrel Jack | - | 1 | - | Row 55: $0.64 (Digikey)
Connector | J_GPS1 | JST-PH 4-pin | - | 1 | - | Solder on assembly
Connector | J_LIM1,J_LIM2 | JST-PH 3-pin | - | 2 | - | Solder on assembly
Connector | J_MOT1,J_MOT2 | JST-XH 4-pin | - | 2 | - | Row 54: incl w/pigtails
Header | J_MP1584 | 1x4 Pin Header | - | 1 | - | For buck module
Socket | J_PI1 | 2x20 Female Header | - | 1 | - | Row 52: $1.42
Socket | J_TMC1,J_TMC2 | 1x8 Female (×4 total) | - | 4 | - | Row 53: $1.61
 |  |  |  | TH Total: | $0.00 | Already in main BOM rows 50-55
Totals: | Includes shipping and tax
Digikey: | $72.69
Aliexpress: | $285.26
Hardware store: | I will pay/find these parts
JLCPCB: | $45.71
Total: | $403.66

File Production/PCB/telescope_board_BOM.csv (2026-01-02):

Comment | Designator | Footprint | LCSC Part Number
100uF 25V | C1 | CP_Radial_D6.3mm_P2.50mm
220uF 10V | C2 | CP_Radial_D8.0mm_P3.50mm
22uF 16V Tantalum | C3 | CP_EIA-3216-18_Kemet-A | C782264
100nF | C4 | C_0603_1608Metric | C14663
100uF 25V | C5 | CP_Radial_D6.3mm_P2.50mm
100uF 25V | C6 | CP_Radial_D6.3mm_P2.50mm
100nF | C7 | C_0603_1608Metric | C14663
100nF | C8 | C_0603_1608Metric | C14663
100nF | C9 | C_0603_1608Metric | C14663
100nF | C10 | C_0603_1608Metric | C14663
100nF | C11 | C_0603_1608Metric | C14663
6.8V Zener | D1 | D_SOD-123 | C2120
4A Polyfuse | F1 | Fuse_2920_7451Metric | C139284
1.5A Polyfuse | F2 | Fuse_1206_3216Metric | C70083
Barrel Jack | J1 | BarrelJack_Horizontal
JST-PH 4P | J_GPS1 | JST_PH_B4B-PH-K_1x04_P2.00mm_Vertical
JST-PH 3P | J_LIM1 | JST_PH_B3B-PH-K_1x03_P2.00mm_Vertical
JST-PH 3P | J_LIM2 | JST_PH_B3B-PH-K_1x03_P2.00mm_Vertical
JST-XH 4P | J_MOT1 | JST_XH_B4B-XH-A_1x04_P2.50mm_Vertical
JST-XH 4P | J_MOT2 | JST_XH_B4B-XH-A_1x04_P2.50mm_Vertical
Pin Header 1x4 | J_MP1584 | PinHeader_1x04_P2.54mm_Vertical
Pin Socket 2x20 | J_PI1 | PinSocket_2x20_P2.54mm_Vertical
TMC2209 Module | J_TMC1 | MODULE_TMC2209_SILENTSTEPSTICK
TMC2209 Module | J_TMC2 | MODULE_TMC2209_SILENTSTEPSTICK
AO3401A | Q1 | SOT-23 | C15127
10k | R1 | R_0603_1608Metric | C25804
10k | R2 | R_0603_1608Metric | C25804
10k | R3 | R_0603_1608Metric | C25804
AMS1117-3.3 | U1 | SOT-223-3_TabPin2 | C6186

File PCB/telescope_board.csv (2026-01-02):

Id | Designator | Footprint | Quantity | Designation | Supplier and ref
1 | F1 | Fuse_2920_7451Metric | 1 | Polyfuse
2 | C1,C5,C6 | CP_Radial_D6.3mm_P2.50mm | 3 | 100µF 25V
3 | C2 | CP_Radial_D8.0mm_P3.50mm | 1 | 220µF 10V
4 | C3 | CP_EIA-3216-18_Kemet-A | 1 | 22µF Tant
5 | C4,C7,C8,C9,C10,C11 | C_0603_1608Metric | 6 | 100nF
6 | D1 | D_SOD-123 | 1 | D_Zener
7 | F2 | Fuse_1206_3216Metric | 1 | Polyfuse
8 | J1 | BarrelJack_Horizontal | 1 | Barrel_Jack_Switch
9 | J_GPS1 | JST_PH_B4B-PH-K_1x04_P2.00mm_Vertical | 1 | JST-PH
10 | J_LIM1,J_LIM2 | JST_PH_B3B-PH-K_1x03_P2.00mm_Vertical | 2 | JST-PH
11 | J_MOT1,J_MOT2 | JST_XH_B4B-XH-A_1x04_P2.50mm_Vertical | 2 | JST-XH
12 | J_MP1584 | PinHeader_1x04_P2.54mm_Vertical | 1 | J_MP1584
13 | J_PI1 | PinSocket_2x20_P2.54mm_Vertical | 1 | Raspberry Pi Zero
14 | J_TMC1,J_TMC2 | MODULE_TMC2209_SILENTSTEPSTICK | 2 | TMC2209_SILENTSTEPSTICK
15 | Q1 | SOT-23 | 1 | AO3401A
16 | R1,R2,R3 | R_0603_1608Metric | 3 | 10k
17 | TP1,TP2,TP3,TP4,TP5,TP6 | TestPoint_Pad_D1.5mm | 6 | TestPoint
18 | U1 | SOT-223-3_TabPin2 | 1 | AMS1117-3.3

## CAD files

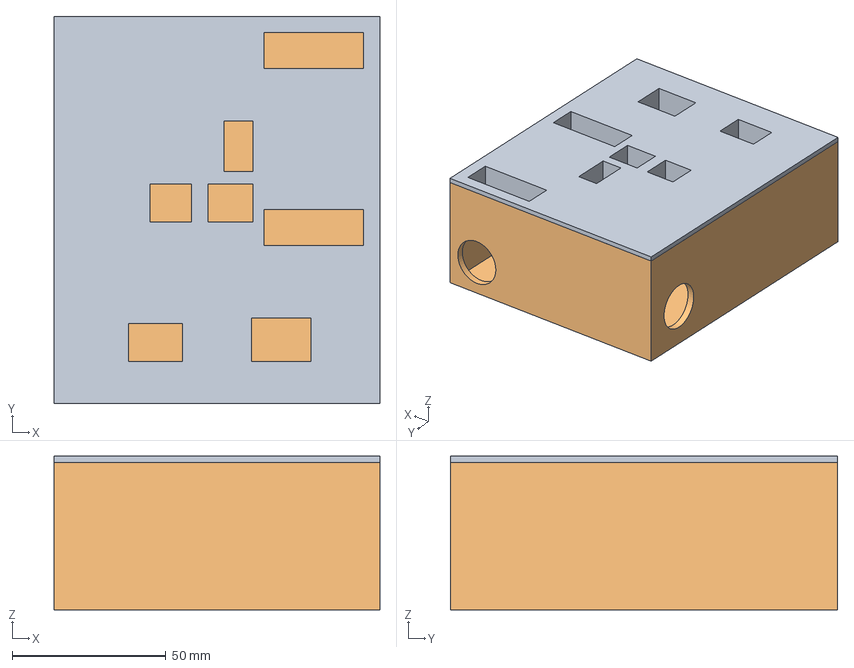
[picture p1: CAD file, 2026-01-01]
Modeling/Electronics/Electronics_Enclosure.step
106.0 x 126.0 x 50.0 mm

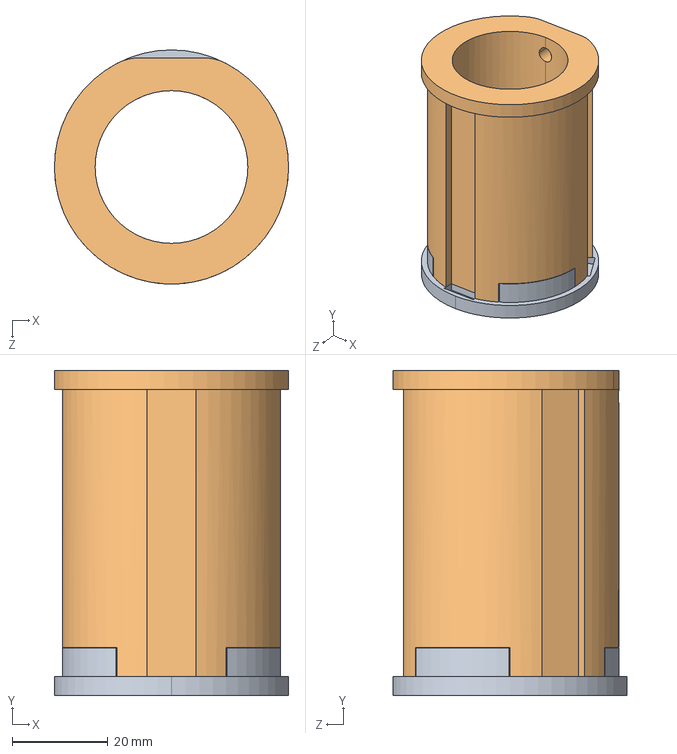
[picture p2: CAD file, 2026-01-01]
Modeling/Focuser/Drawtube 60mm.STEP
49.0 x 68.0 x 49.0 mm

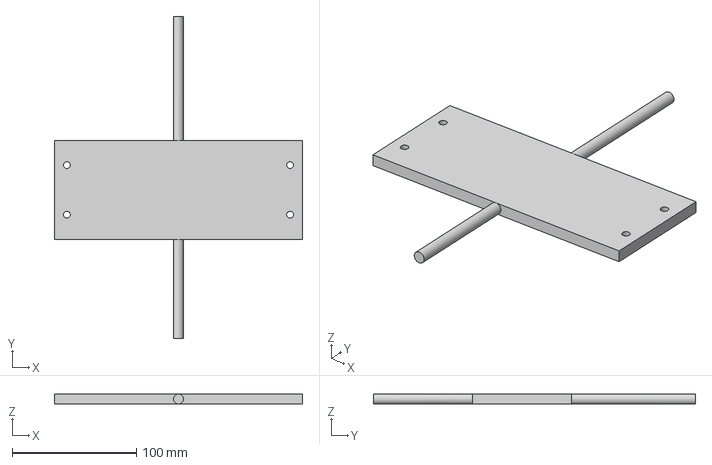
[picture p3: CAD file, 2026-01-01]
Modeling/Mount/Altitude_Cradle.step
200.0 x 260.0 x 8.00 mm

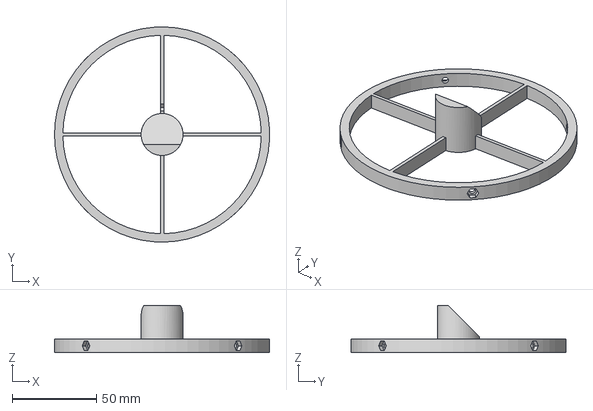
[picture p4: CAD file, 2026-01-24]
Modeling/OTA/Secondary_Spider.step
127.9 x 128.0 x 28.0 mm

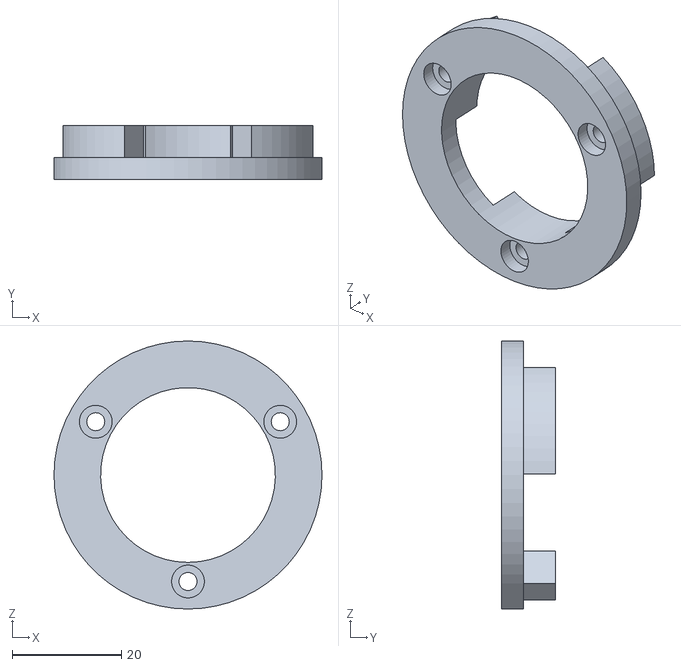
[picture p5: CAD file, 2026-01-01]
Production/3d print/Focuser/Drawtube cap.STL
49.0 x 9.90 x 49.0

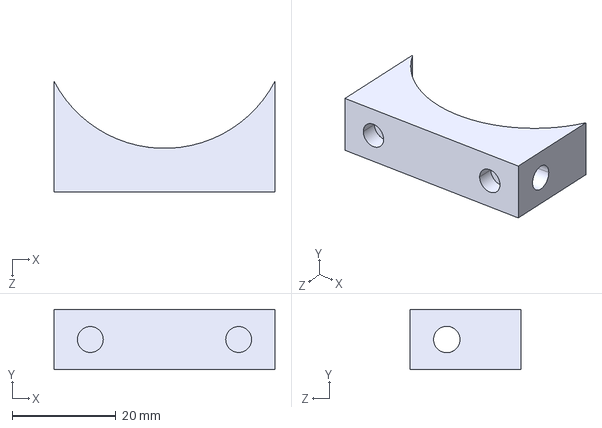
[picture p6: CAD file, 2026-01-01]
Modeling/Focuser/Pinion block.STEP
42.6 x 11.6 x 21.3 mm

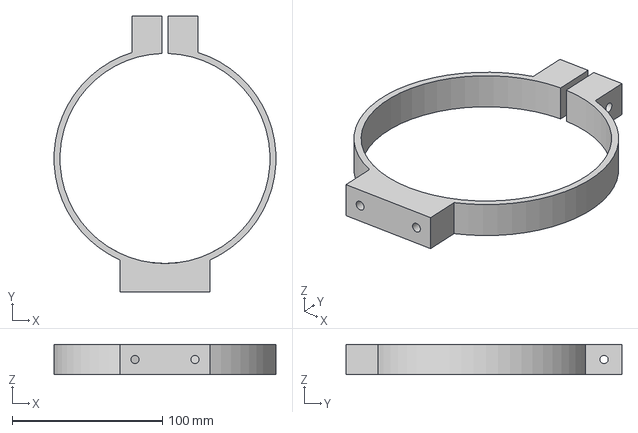
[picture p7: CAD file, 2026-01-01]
Modeling/Mount/Tube_Rings.step
147.8 x 184.0 x 20.0 mm

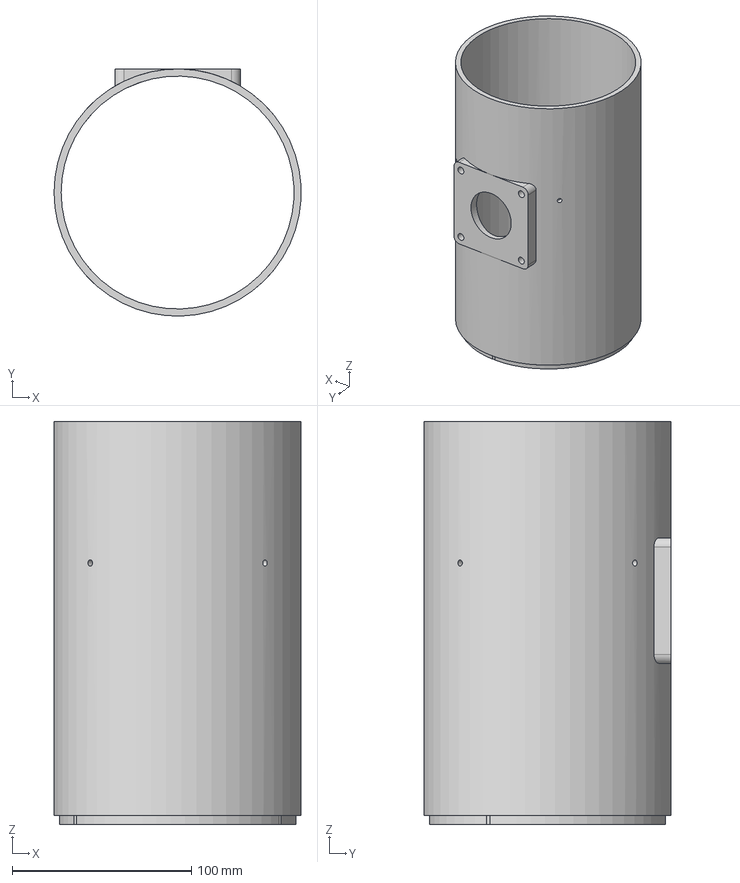
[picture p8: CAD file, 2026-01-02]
Modeling/OTA/Tube_Segment_4_Focuser.step
137.9 x 138.0 x 225.0 mm

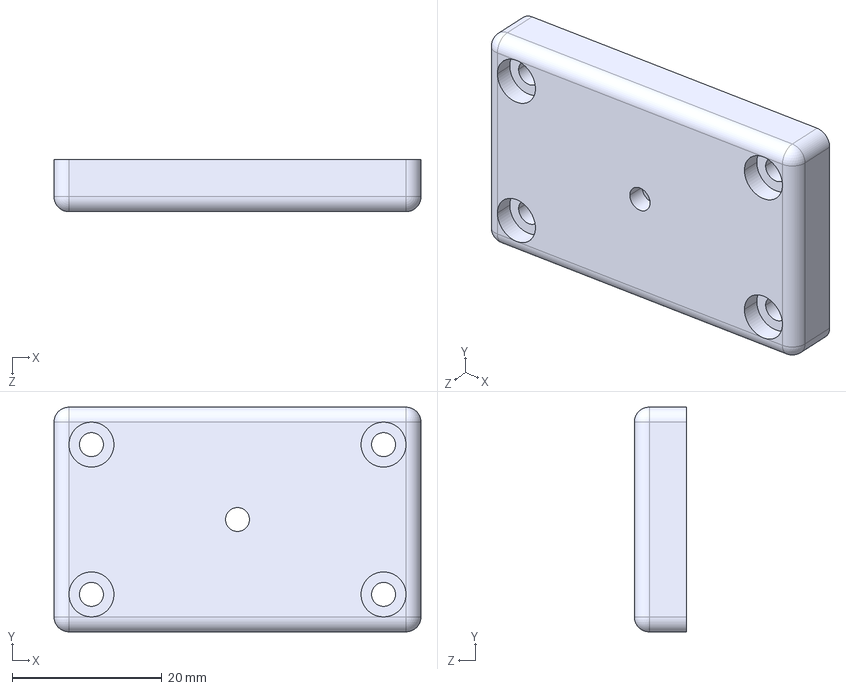
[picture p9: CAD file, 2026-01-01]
Modeling/Focuser/Front cap.STEP
49.0 x 30.0 x 7.00 mm

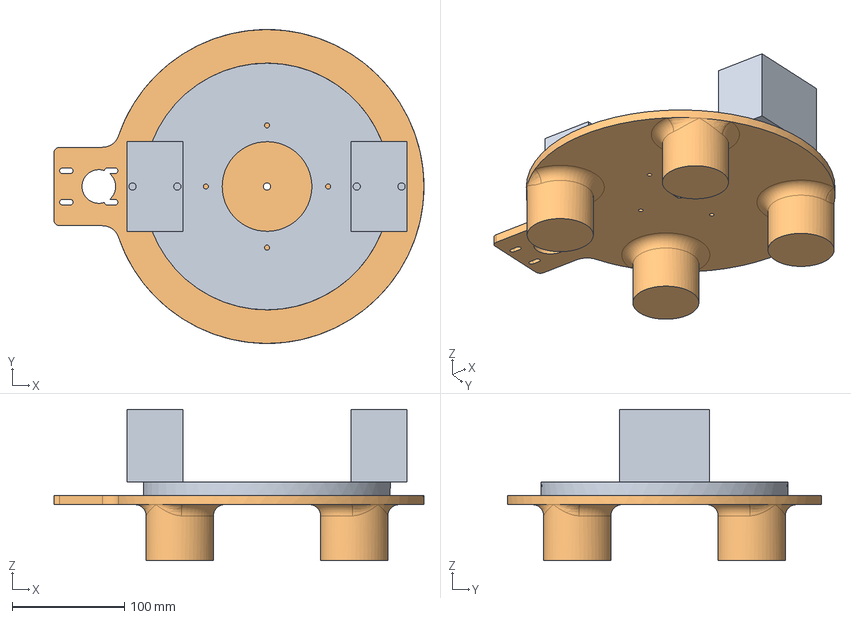
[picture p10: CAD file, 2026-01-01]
Modeling/Mount/Azimuth_Stationary_Base.step
330.0 x 280.0 x 135.0 mm

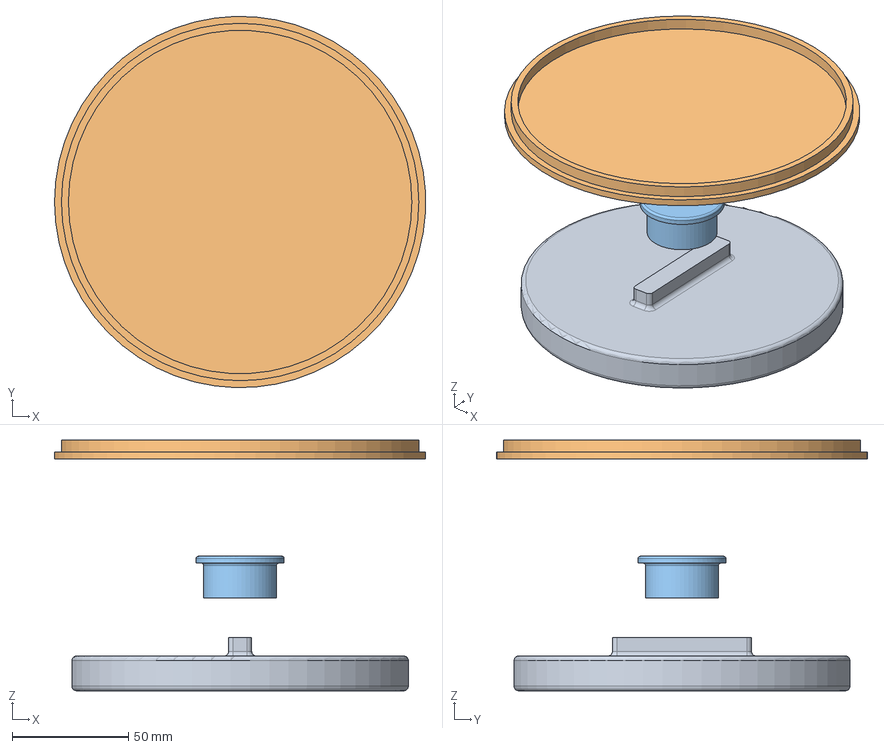
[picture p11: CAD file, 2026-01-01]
Modeling/OTA/Caps.step
159.9 x 159.9 x 108.0 mm
Front_Dust_Cap
Rear_Dust_Cover
Focuser_Cap

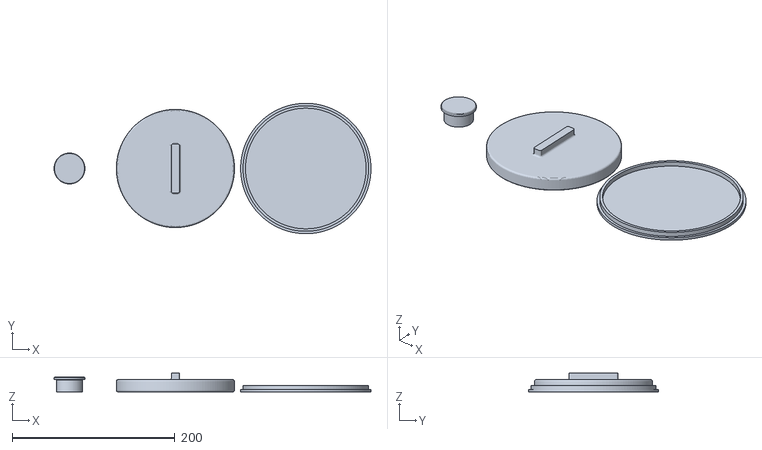
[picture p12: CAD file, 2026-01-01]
Production/3d print/Caps.stl
389.0 x 160.0 x 23.0

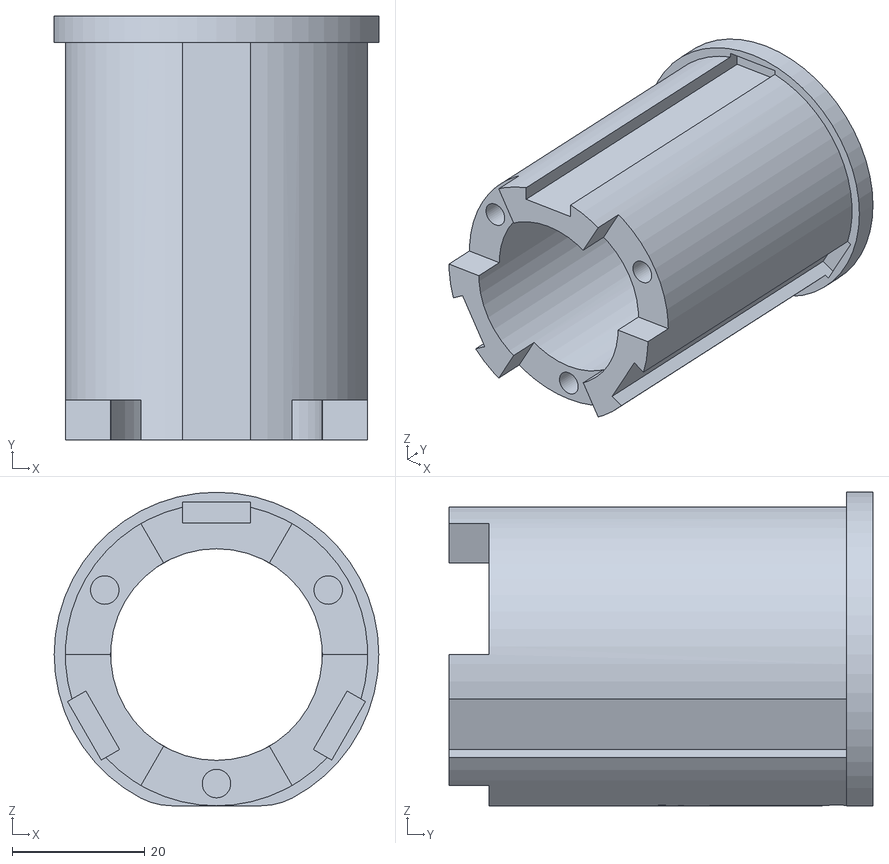
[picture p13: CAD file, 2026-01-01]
Production/3d print/Focuser/Drawtube 60mm.STL
49.0 x 64.0 x 47.3

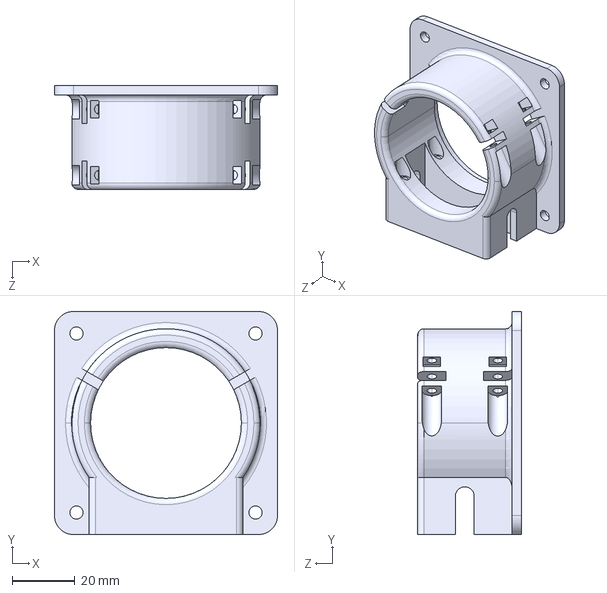
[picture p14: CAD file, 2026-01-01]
Modeling/Focuser/Base.STEP
71.0 x 71.0 x 33.0 mm

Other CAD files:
Production/3d print/Secondary_Spider.stl
Production/3d print/Focuser/Focuser - Pinion block-1.STL
Production/3d print/Tube_Segment_4_Focuser.stl
Modeling/Mount/Altitude_Fork.step
Modeling/Mount/Alt_Motor_Mount.step
Modeling/Mount/Altitude_Fork_Left.step
Modeling/OTA/Primary_Mirror_Cell.step
Modeling/OTA/Tube_Segment.step
Modeling/OTA/Tube_Segment_1_Primary.step
Modeling/Reference/GT2 Pulley Misumi Shape B 60T.step
Production/3d print/Alt_Motor_Mount.stl
Production/3d print/Altitude_Cradle.stl
Production/3d print/Altitude_Fork.stl
Production/3d print/Altitude_Fork_Left.stl
Production/3d print/Azimuth_Stationary_Base.stl
Production/3d print/Electronics_Enclosure.stl
Production/3d print/Focuser/Focuser - Base-1.STL
Production/3d print/Focuser/Focuser - Front cap-1.STL
Production/3d print/Focuser/Knob.STL
Production/3d print/Focuser/Pinion spacer.STL
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

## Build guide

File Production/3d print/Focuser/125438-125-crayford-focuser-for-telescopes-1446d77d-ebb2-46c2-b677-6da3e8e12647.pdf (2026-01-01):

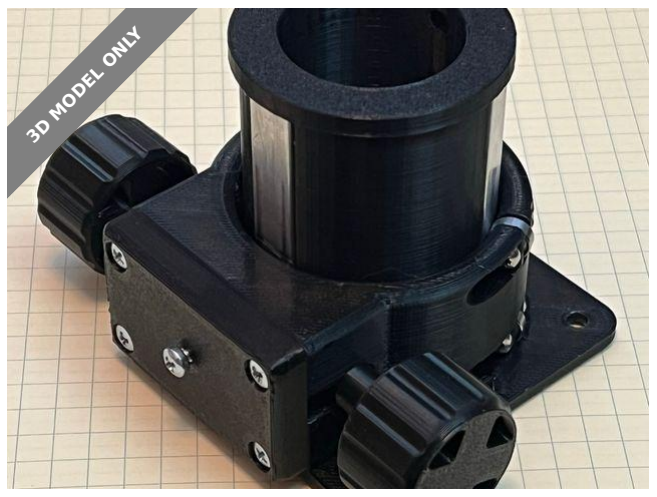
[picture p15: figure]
3D MODEL ONLY

## Summary

DIY 1.25 Crayford focuser

Learning (https://printables.com/model?categoryId=90) > | Physics & Astronomy (https://printables.com/model?categoryId=91)
Tags: telescope | focuser | crayford

This focuser was made to use with my Skywatcher Heritage 130P. The

mounting holes are 57mm spacing, which matches the secondary piece I

made here: https://www.prusaprinters.org/prints/122949-skywatcher-

heritage-130p-secondary-piece-remix (https://www.prusaprinters.org/prints/122949-skywatcher-heritage-130p-secondary-piece-remix)

The focuser itself is similar to a bunch of other designs I saw online but is

not a remix. The drawtube is a new approach, rather than stick metal

pieces to flat sides of a tube this uses pieces of aluminium inserted into

slots in the top and bottom of the tube. When the tube is assembled then

the metal bearing surfaces are captive with no glue. I used 10x3mm

aluminium extrusion 64mm long. (If you can accurately cut flat pieces of

steel that would be better) The drawtube is assembled using M3 brass

inserts and 12mm M3 bolts. It must be assembled when in the main tube.

The main piece has four 3x8x3 bearings held in place with a 10mm M3

bolt and a M3 nylock nut. It has four M3 brass inserts for the 20mm M3

front cap bolts to engage.

aeberbach (https://printables.com/@aeberbach)

## 1.25" Crayford

## Focuser for

## telescopes

VIEW IN BROWSER (https://printables.com/model/125438-125-crayford-focuser-for-telescopes)

updated 7. 11. 2023 | published 7. 11. 2023

The pinion is a 90mm long stainless steel shaft 5mm in diameter. It passes

through the pinion block and is pressed against the front bearing surface.

In the back of the pinion block are two holes for springs, that are

compressed by the tension plate - a piece of the same 10x3mm aluminium

as the bearing surfaces, this time 37mm long. These springs are 6.5mm

uncompressed, 3.5mm compressed, a bit under 5mm in diameter. Pen

springs are not quite strong enough. The tension is adjusted by the central

bolt in the front cap, threaded through the inserted M3 hex nut, which

compresses the springs and pushes the pinion against the front bearing

surface. A thumbscrew here would be ideal - very similar to the ones used

on the Boss guitar pedals are what you need.

(An earlier design used bearings on the pinion shaft but more friction here

is good; with bearings the focuser would not hold much weight as it

rotates too freely)

Once everything is printed (I used Prusament PETG, 0.2 layer height with

0.4mm nozzle) and the supports cleared off begin by inserting the

bearings into the body with the locknuts. Don't overtighten. Next put the

pinion shaft through the bearing block - make sure the pinion is cut cleanly

and the ends slightly chamfered with a file to make insertion easier. The

pinion block might need a slight sand to enter the main body easily

depending on your print quality. Also get the M3 brass inserts for the front

cap bolts inserted.

Insert the M3 hex nut into the matching recess inside the front cap. With

the front cap facing down put the tension block in the slot, then springs,

then pinion block - insert this all in the main body as one unit keeping the

springs and plate in place. As you tighten the four bolts to hold the front

cap in place be sure the tension plate is in its slot and the spring are in the

holes, this should not be hard to assemble but you might want to poke it

with a small screwdriver from the side to adjust part positions as the front

bolts are tightened. This is the only hard part of assembly - see final photo

with springs sandwiched between plate and block for correct assembly

position.

Then the drawtube can be assembled. There are two STL files, one for the

tube itself and one for the cap. Orient both with the flange toward the print

surface in the slicer. Add M3 inserts to this also and one M4 insert near the

flat part of the top flange to hold a thumbscrew to secure the eyepiece.

Take the three bearing surface plates and insert them in the slots in the

large part. Insert the drawtube into the main body so that the bearings run

on two plates and the pinion runs on one, then add the cap so that the

plates enter the slots in the cap. The flat part with the eyepiece screw

faces away from the pinion. Then add the drawtube cap, secured by 3

bolts, and the drawtube is locked in place. Find yourself a nylon M4

thumbscrew if possible to secure eyepieces.

# Model files

Finally you can cover the metal of the shaft that sticks out of the main

body with one of the pinion spacers per side and then add a knob each

side, The knobs are a tight fit but a hole for a M4 insert is provided, you

can also file the end of the pinion a little flat to help with engagement.

15 August 23: I have added STEP files for the printable parts. For the focus

wheels I recommend you make your own - sorry but I have misplaced the

original files! If you want to use the STEP files then likely you know how to

do this already.

Clear skies!

focuser-pinion-block-1.stl

pinion-spacer.stl

knob.stl

focuser-front-cap-1.stl

focuser-base-1.stl

drawtube-60mm.stl

## License

This work is licensed under a

Creative Commons (4.0 International License)

Attribution-NonCommercial (http://creativecommons.org/licenses/by-nc/4.0/)

✖ | Sharing without ATTRIBUTION
✔ | Remix Culture allowed
✖ | Commercial Use
✖ | Free Cultural Works
✖ | Meets Open Definition

drawtube-cap.stl

pinion-block.step

front-cap.step

drawtube-60mm.step

base.step

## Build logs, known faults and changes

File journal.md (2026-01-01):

<!--
  This journal is auto generated by Hack Club Blueprint.
-->

## 12/23/2025 - Lots of placements, reading and designing, and some design  

_Time spent: 3.5h_  

I've been inspired! I spent a few hours researching the components, doing some quick calculations, and reading spec sheets.
I'm now ready to start on my PCB, which will sorta be like a carrier board for a RP zero 2. 
Hopefully I can get that component done in a few days, and then work on CAD modeling for the actual telescope! 

## 12/24/2025 6 PM - Design done, components assigned!  

_Time spent: 4.0h_  





I finished up designing the PCB, and assigned footprints for every part! Took a lot of back and forth researching, but I think I have EVERYTHING I need, 100% correct. Ready to start actual PCB design!!

## 12/24/2025 10 PM - Started power management  

_Time spent: 1.0h_  



Started just laying out the power input and managing components, tbh, most of this board is about that, and just making sure we can drive the motors needed to rotate the telescope.   

## 12/25/2025 1 PM - PCB Done  

_Time spent: 5.0h_  





PCB is done! made a few more tweaks to the design to have the right symbols and footprints, and laid out everything where it belongs!
As the voltage and heat generated is pretty high, the ground fills needed to have enough copper mass for this board are quite large. 
I may end up having to add a heatsink, we will see. 

## 12/25/2025 10 PM - Started CAD design  

_Time spent: 2.0h_  



Spent a while going back and forth, and re learning CAD. There will be 4 of these segments, segments 2&3 will just be this, segment 4 (the top) will have the aperture and primary lens, segment 1 will have the secondary lens and the camera system. 

Additional things to design will be the electronics box, several rings to clamp on, lens mounts, and a stand

## 12/26/2025 12 PM - Unique segments done  

_Time spent: 2.0h_  



Modules 1 & 4 (the end pieces) are in! One of them has six holes for heat set screws, and the other one has a hole for mounting the primary focusing mirror.
I'm really bad at cad lolol  

## 12/26/2025 2 PM - Primary mirror cell  

_Time spent: 1.0h_  



Finished CAD modeling the primary mirror holder!
It'll be holding this mirror: https://www.aliexpress.us/item/3256802406856110.html?gatewayAdapt=glo2usa4itemAdapt#nav-specification

I think it shouldddd fit, gonna have to make some clips to hold the mirror down, but theres also slots for the colimitation (basically just fancy word for alignment) screws.

Ideal vision is the screws tilt it into alignment, and then the clips keep it there while the telescope moves  

## 12/26/2025 10 PM - Secondary mirror holder  

_Time spent: 2.5h_  



By far the most complex thing I have modeled so far, it's not too bad, but took a lot of research and iteration. the mirror will be glued on, so hopefully we can use the 25mm that comes with the set im buying. 

Photo of alignment testing with section 4:


## 12/27/2025 9 AM - Minor alignment tweak  

_Time spent: 0.5h_  



Spent some time rotating components by 45 degrees in order to ensure that the bolts would be away from the main opening for the focuser, also researched and found a 3d model of a focuser online! (precision optics is beyond me)  

## 12/27/2025 10 AM - Mount designed for eyepiece/focuser  

_Time spent: 1.0h_  



This took forever cuz i had to swap quite a few times! As it turns out, most focusers are designed for a curved body, and so I spent quite a while trying and failing to make a curved boss, anyways, I found this 3d printed one, which should both save cost, and lets me have a much simpler flat boss!  

## 12/27/2025 9 PM - re did the primary mirror cell :(  

_Time spent: 4.0h_  



Yup, screenshot of shame, idk, ive spent probably a solid 8 hours on this, im listing 4 cuz that seems more honest (reels may have been scrolled)

anyways uhh yeah i redid this like 5 different ways and was considering just stealing the hadley's design (cuz its good) but no. so now we have a proper floating plate setup, and ive got quite a few more parts in the bom.

gonna go work on simple stuff tomorrow morning to get warmed up, then jump into the mount, which is hopefully the last thing. 

## 12/28/2025 3 PM - Caps  

_Time spent: 1.0h_  

Late start today, got back into it by modeling the 3 different plugs/caps. Took some time as I intend to do friction fit, so I had to load up various models, i also did a test assembly of the telescope to make sure stuff is fitting and logical. 


## 12/28/2025 7 PM - Electronics box  

_Time spent: 1.0h_  



Fooled around for a while on how I wanted to do this, and then just decided to keep it simple.
There's no need to extreme precision here, it's just to organize the electronics.   

## 12/28/2025 10 PM - Mounting hardware  

_Time spent: 2.0h_  







Based on my research, i have designed a system that uses two rings, a plate to basically hold the rings together, and then two forks which attach to the plate. 
next up is the rotating base, and motor attachments, and then we're kinda done lol

## 12/29/2025 9 AM - Continued work on mount  

_Time spent: 2.0h_  



Found a lazy suzan bearing online to use, and started designing mount to interface with it. I really really hope i have these measurements correct, as the seller is not very clear on the specs, if all else fails, there are other means of mounting it lol

## 12/29/2025 3 PM - Mounting plate and attitude fork adjustments and other stuff  

_Time spent: 2.5h_  




Found a motor WITH a worm gear, made a mounting plate for it, and then updated the attitude fork. Then, after reading some stuff online, i realized its a really bad idea to do close fit holes when 3d printing, cuz the material can contract, so I had to go through and swap everything out for normal fit, including some of the hexagons, which are inscribed inside circles, which is all just extra fun.   

## 12/29/2025 5 PM - Motor mounts are actually correct now  

_Time spent: 2.0h_  



. 

Using like a pulley thing for the azimuth, had to update both of them to use slots cuz turns out, they need to be slots.

Ended up doing a ton of research work cuz i have no idea whats going on here, and now i have a mount that I think SHOULD fit...

## 12/29/2025 9 PM - Feet, and about a billion small fixes  

_Time spent: 2.0h_  



Added some feet! Will add friction pads here. Also changed more dumb stuff, such as wrong motor mounts, backwards joints, ect ect, all just logic things or stuff that hadn't been updated.
Gonna do a full test build tomorrow, and hopefully ship.   

## 12/30/2025 - Did a test assembly  

_Time spent: 2.0h_  



Assembled all the parts together! Found a bunch more issues with the design... anyways, they're all fixed now! Hoping to get everything together into a BOM, and submit production files today for review!  

## 1/1/2026 - Assembled bom and final stuff  

_Time spent: 5.0h_  




Final assembly of everything, really took FOREVER cuz i had to find everything on aliexpress, im gonna be buying a lot from my local hardware store, hopefully the grant covers that.

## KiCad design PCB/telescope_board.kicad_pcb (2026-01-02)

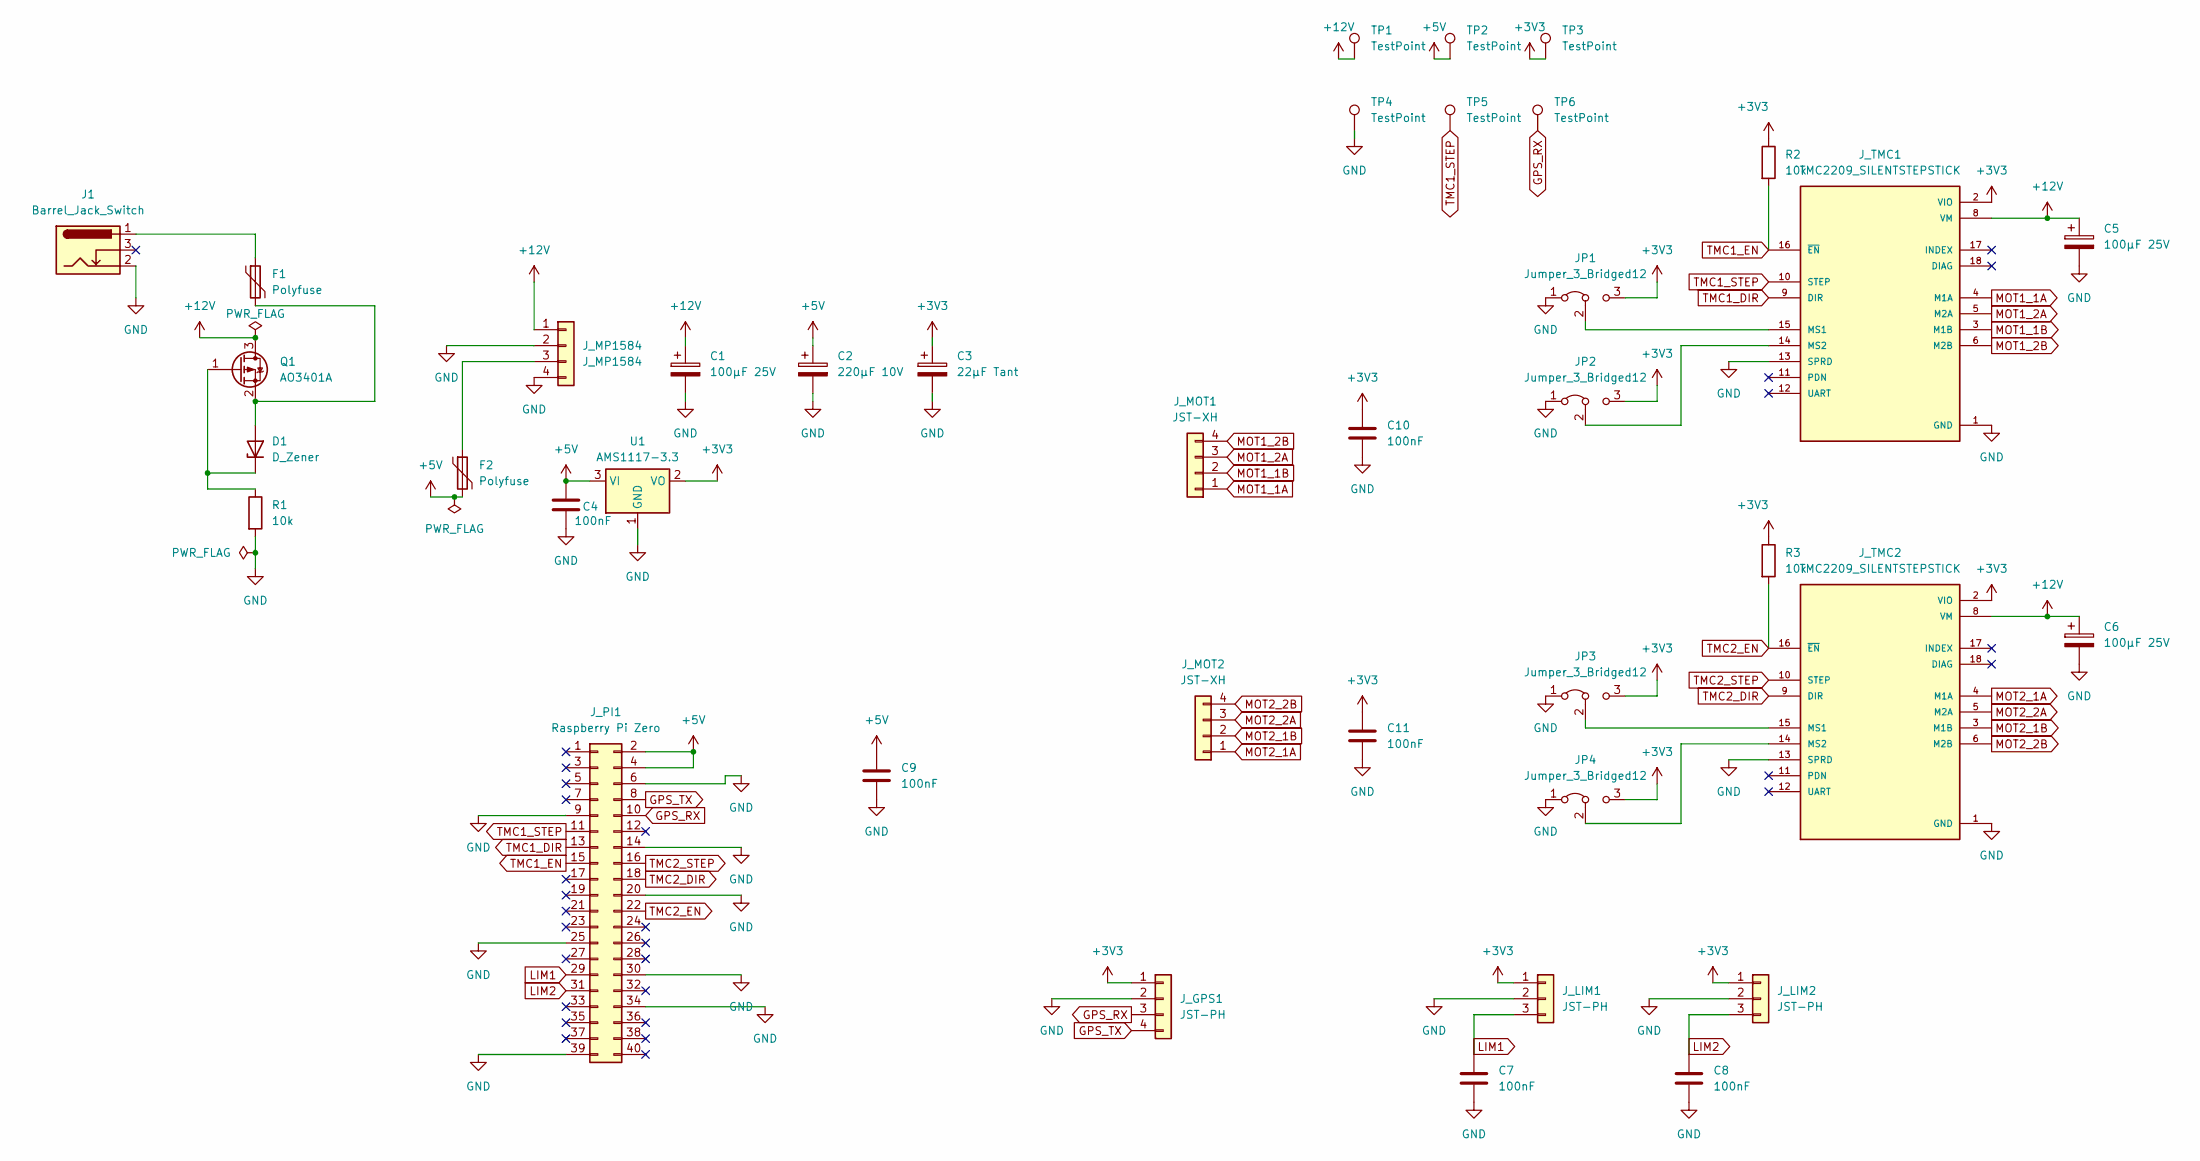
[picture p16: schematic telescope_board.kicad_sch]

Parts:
C1, C5, C6: 100µF 25V; CP_Radial_D6.3mm_P2.50mm
C2: 220µF 10V; CP_Radial_D8.0mm_P3.50mm
C3: 22µF Tant; CP_EIA-3216-18_Kemet-A
C4, C7, C8, C9, C10, C11: 100nF; C_0603_1608Metric
D1: D_Zener; D_SOD-123
F1: Polyfuse; Fuse_2920_7451Metric
F2: Polyfuse; Fuse_1206_3216Metric
J1: Barrel_Jack_Switch; BarrelJack_Horizontal
JP1, JP2, JP3, JP4: Jumper_3_Bridged12; SolderJumper-3_P1.3mm_Bridged12_RoundedPad1.0x1.5mm
J_GPS1: JST-PH; JST_PH_B4B-PH-K_1x04_P2.00mm_Vertical
J_LIM1, J_LIM2: JST-PH; JST_PH_B3B-PH-K_1x03_P2.00mm_Vertical
J_MOT1, J_MOT2: JST-XH; JST_XH_B4B-XH-A_1x04_P2.50mm_Vertical
J_MP1584: J_MP1584; PinHeader_1x04_P2.54mm_Vertical
J_PI1: Raspberry Pi Zero; PinSocket_2x20_P2.54mm_Vertical
J_TMC1, J_TMC2: TMC2209_SILENTSTEPSTICK; MODULE_TMC2209_SILENTSTEPSTICK; PARTREV 1.20
Q1: AO3401A; SOT-23
R1, R2, R3: 10k; R_0603_1608Metric
TP1, TP2, TP3, TP4, TP5, TP6: TestPoint; TestPoint_Pad_D1.5mm
U1: AMS1117-3.3; SOT-223-3_TabPin2

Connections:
+3V3: C3.1, C10.1, C11.1, JP1.3 (B), JP2.3 (B), JP3.3 (B), JP4.3 (B), J_GPS1.1, J_LIM1.1, J_LIM2.1, J_TMC1.2 (VIO), J_TMC2.2 (VIO), R2.1, R3.1, TP3.1, U1.2 (VO)
+5V: C2.1, C4.1, C9.1, F2.2, J_PI1.2, J_PI1.4, TP2.1, U1.3 (VI)
+12V: C1.1, C5.1, C6.1, J_MP1584.1, J_TMC1.8 (VM), J_TMC2.8 (VM), Q1.3 (D), TP1.1
GND: C1.2, C2.2, C3.2, C4.2, C5.2, C6.2, C7.2, C8.2, C9.2, C10.2, C11.2, J1.2, JP1.1 (A), JP2.1 (A), JP3.1 (A), JP4.1 (A), J_GPS1.2, J_LIM1.2, J_LIM2.2, J_MP1584.2, J_MP1584.4, J_PI1.6, J_PI1.9, J_PI1.14, J_PI1.20, J_PI1.25, J_PI1.30, J_PI1.34, J_PI1.39, J_TMC1.1 (GND), J_TMC1.7 (GND), J_TMC1.13 (SPRD), J_TMC2.1 (GND), J_TMC2.7 (GND), J_TMC2.13 (SPRD), R1.2, TP4.1, U1.1 (GND)
GPS_RX: J_GPS1.3, J_PI1.10, TP6.1
GPS_TX: J_GPS1.4, J_PI1.8
LIM1: C7.1, J_LIM1.3, J_PI1.29
LIM2: C8.1, J_LIM2.3, J_PI1.31
MOT1_1A: J_MOT1.1, J_TMC1.4 (M1A)
MOT1_1B: J_MOT1.2, J_TMC1.3 (M1B)
MOT1_2A: J_MOT1.3, J_TMC1.5 (M2A)
MOT1_2B: J_MOT1.4, J_TMC1.6 (M2B)
MOT2_1A: J_MOT2.1, J_TMC2.4 (M1A)
MOT2_1B: J_MOT2.2, J_TMC2.3 (M1B)
MOT2_2A: J_MOT2.3, J_TMC2.5 (M2A)
MOT2_2B: J_MOT2.4, J_TMC2.6 (M2B)
unnamed: D1.2 (A), F1.2, Q1.2 (S)
unnamed: D1.1 (K), Q1.1 (G), R1.1
unnamed: F1.1, J1.1
unnamed: JP1.2 (C), J_TMC1.15 (MS1)
unnamed: JP2.2 (C), J_TMC1.14 (MS2)
unnamed: JP3.2 (C), J_TMC2.15 (MS1)
unnamed: JP4.2 (C), J_TMC2.14 (MS2)
unnamed: F2.1, J_MP1584.3
TMC1_DIR: J_PI1.13, J_TMC1.9 (DIR)
TMC1_EN: J_PI1.15, J_TMC1.16 (~EN), R2.2
TMC1_STEP: J_PI1.11, J_TMC1.10 (STEP), TP5.1
TMC2_DIR: J_PI1.18, J_TMC2.9 (DIR)
TMC2_EN: J_PI1.22, J_TMC2.16 (~EN), R3.2
TMC2_STEP: J_PI1.16, J_TMC2.10 (STEP)

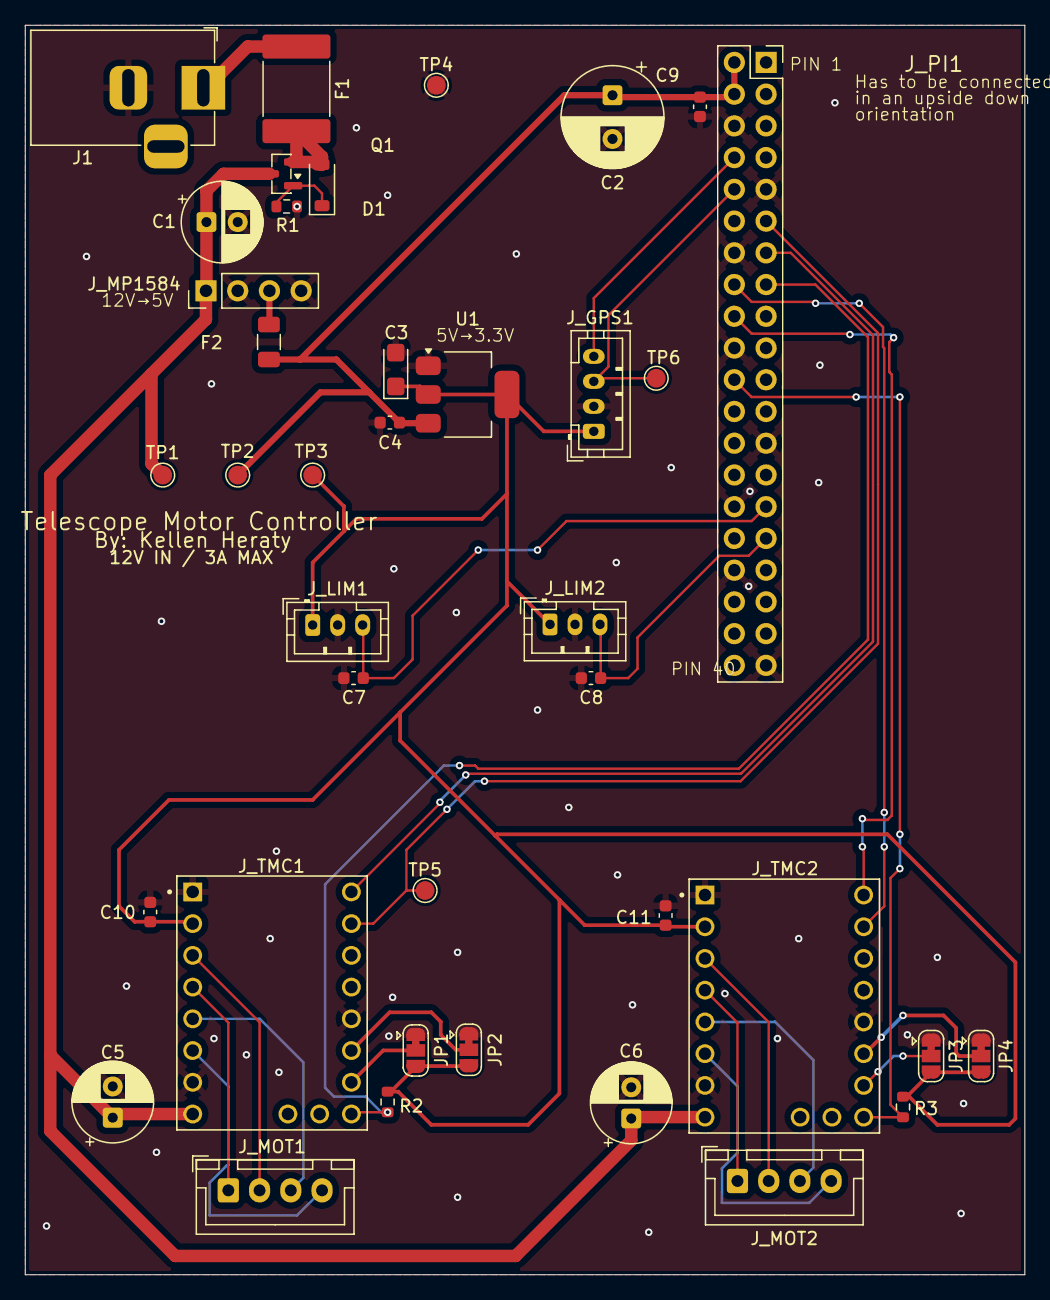
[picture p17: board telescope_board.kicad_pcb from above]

Board: 2 copper layers, 80.0 x 100.0 mm, 39 parts (0 on the bottom side), 30 nets.

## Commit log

2025-12-25 the PCB
    [telescope_board.kicad_pcb, telescope_board.kicad_sch]
2026-01-01 pcb files
2026-01-01 source files and software
    [Alt_Motor_Mount.step, Altitude_Cradle.step, Altitude_Fork.step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]
2026-01-01 quick spec update
    [Secondary_Spider.step]
2026-01-01 added stl files for printing
    [Alt_Motor_Mount.stl, Altitude_Cradle.stl, Altitude_Fork.stl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]
2026-01-01 pcb prod files
    [telescope_board.csv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]
2026-01-01 bom fix
    [telescope_board-top-pos.csv]
2026-01-02 minor adjust to focuser
    [Tube_Segment_4_Focuser.step, Tube_Segment_4_Focuser.stl]
2026-01-02 fixed a math error
    [Tube_Segment_4_Focuser.step, Tube_Segment_4_Focuser.stl]
2026-01-06 Enhance README with assembly images and diagrams
    Added images and diagrams for PCB, CAD, and annotated diagram in the assembly section.
2026-01-09 Enhance README with annotated CAD and component details
    Added annotated CAD details and images for components and connections.
2026-01-24 fix spider
    [Secondary_Spider.step, Secondary_Spider.stl]
